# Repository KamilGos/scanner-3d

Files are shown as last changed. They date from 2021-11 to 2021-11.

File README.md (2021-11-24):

<!-- image -->
<div align="center" id="top"> 
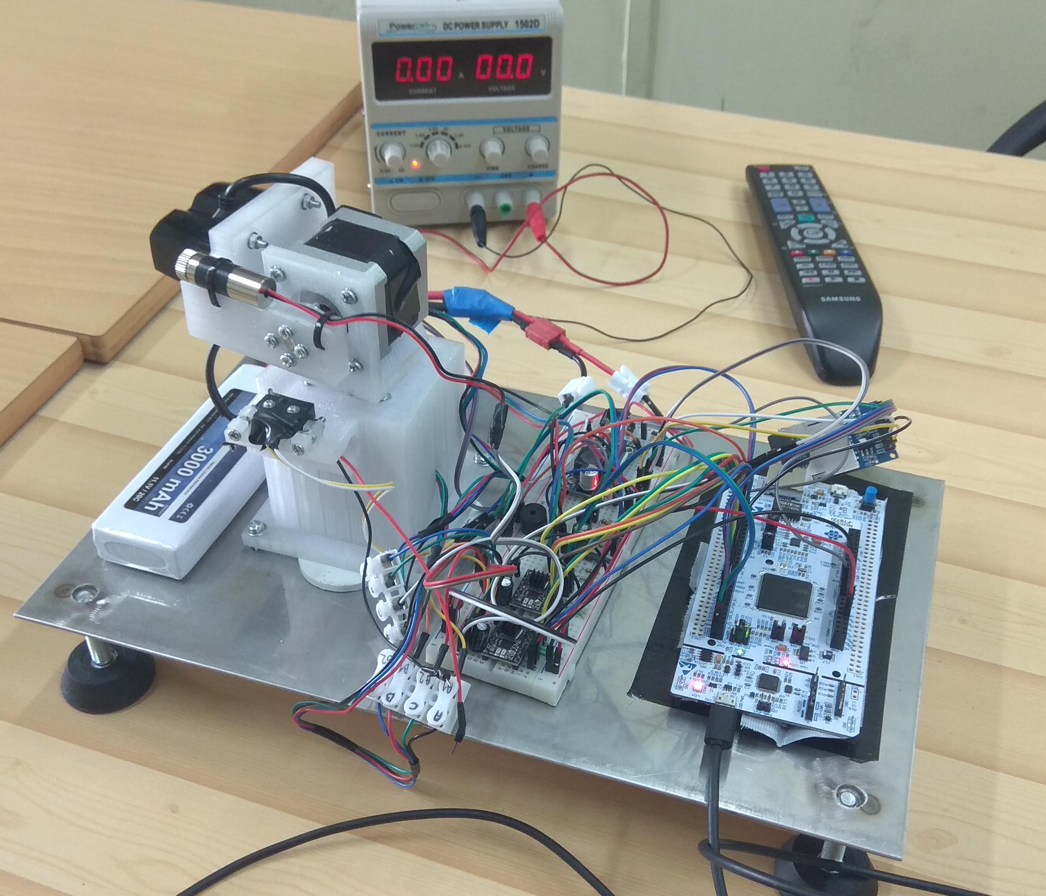
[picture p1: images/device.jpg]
  
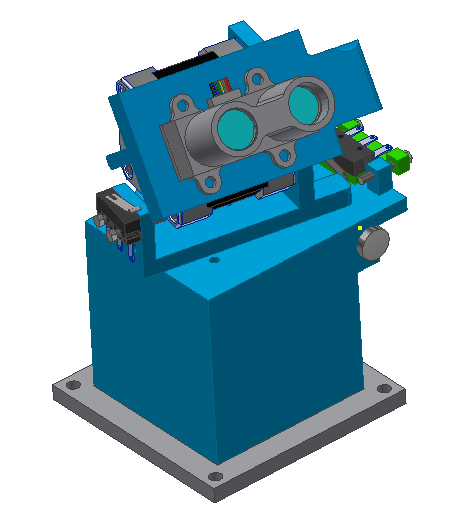
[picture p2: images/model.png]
  
  &#xa0;
</div>

<h1 align="center"> scanner-3d </h1>
<h2 align="center"> Lidar-based 3D environment scanner - generate a point cloud! </h2>

<!-- https://shields.io/ -->
<p align="center">
  
  
  
</p>

<!-- table of contents -->
<p align="center">
  <a href="#dart-about">About</a> &#xa0; | &#xa0;
  <a href="#package-content">Content</a> &#xa0; | &#xa0;
  <a href="#eyes-implementation">Implementation</a> &#xa0; | &#xa0;
  <a href="#microscope-tests">Tests</a> &#xa0; | &#xa0;
  <a href="#memo-license">License</a> &#xa0; | &#xa0;
  <a href="#technologist-author">Author</a> &#xa0; | &#xa0;
</p>

<br>

## :dart: About ##
The aim of the project is to create a device that allows scanning any surface to 3d model.

The process is based on spot distance measurement. To measure the distance the lidar is used. It ensures sufficient accuracy and the range of measurements. 

The basic structure consists of a Lidar mounted on the effector of a manipulator with two degrees of freedom. The whole electronics is based on a static metal structure. The measurements are visualized in a computer application which also provides necessary operations such as Poisson reconstruction. 

<h2>Principle of operation</h2>
The manipulator consists of two degrees of freedom, each rotating by 180 degrees, which allow the measurement of the semi-spherical space above the device. The active element ensuring the rotation of each axis is a stepper motor. Measurements are performed on average every 2ms. Each time after receiving a measurement from Lidar, the microcontroller converts the obtained distance, taking into account the angular position of the effector, into Cartezian coordinate system. The angles that are used to convert the values are updated with each rotation of the shaft of any motor. After the measurement process is completed, the data is transferred to a stationary station, where one make an initial decimation by removing gross errors with the help of a script. Subsequently, using an open-source program (like https://www.meshlab.net/ ), it is possible determine normal vectors for each measurement point, thanks to which we are able to use Poisson smoothing to reconstruct the measurement surface.

<br>

<div align="center" id="top"> 
  
  &#xa0;
</div>

<br>

## :package: Content
 * [CAD/3d_printing](CAD/3d_printing) - STL files for 3d-printing
 * [CAD/sacnner.stp](CAD/scanner.stp) - STEP file with model
 * [examples](examples) - two exmaple files with point clouds genereted with described device
 * [schematic](schematic) - pdf and sch schematics of electronics model
 * [sources](sources) - code for microcontroller

## :eyes: Implementation ##
The mapping algorithm can be explained in the following way:

1. The upper motor takes steps until the upper limit switch sends a signal to the microcontroller. It goes back and performs micro-steps until the upper limit switch sends a signal to the microcontroller for precise alignment.
2. The lower motor does the same as the upper motor for the lower limit switch.
3. The lower motor performs 1 micro step.
4. The top motor performs 1 micro step.
5. Lidar takes a distance measurement and sends it to the microcontroller.
6. Converting distances to coordinates (x, y, z) in the microcontroller
7. The upper motor carries out the remaining micro-steps by performing steps 5 and 6 of the algorithm.
8. Measurements are saved on the SD card in the format (x, y, z).
9. The lower motor carries out the remaining micro-steps by performing steps 3-8

## :microscope: Tests ##
Many scans have been performed, which indicate that the device makes sense and its further development may bring beneficial results. The scans from the examples folder are presented below:

<h2>Example 1 - part of room<h2>
<div align="center">

| Name | Figure |
|--- | --- |
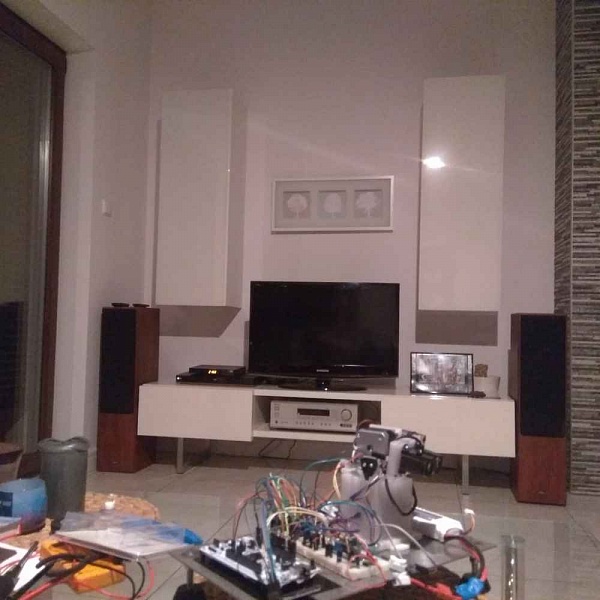
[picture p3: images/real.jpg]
| Real view  |   |
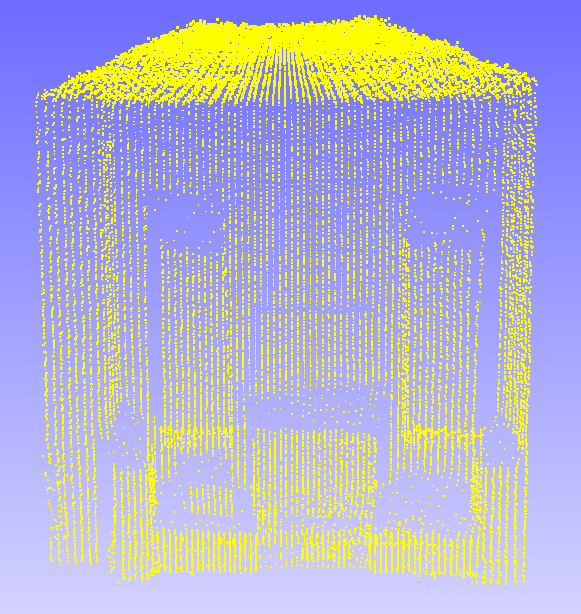
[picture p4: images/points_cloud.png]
| Points cloud  |   |
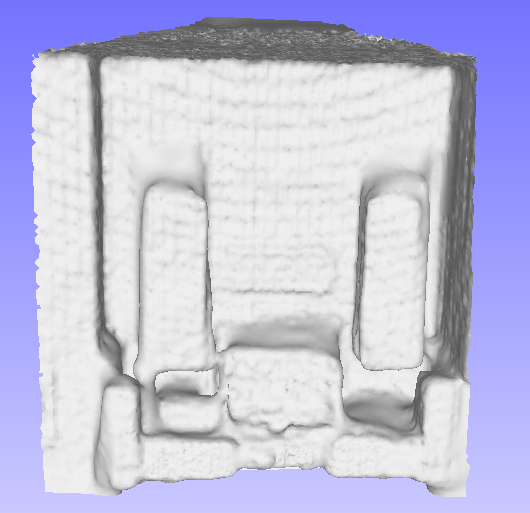
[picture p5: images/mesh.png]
| Poisson reconstruction  |   |
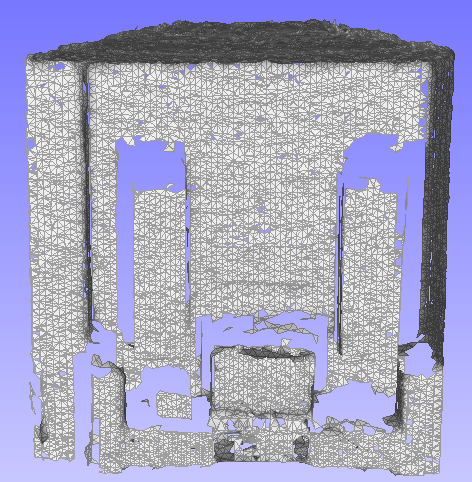
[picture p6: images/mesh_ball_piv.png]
| Ball pivoting reconstruction|   |

</div>

<h2>Example 2 - whole room<h2>
<div align="center">

| Name | Figure |
|--- | --- |
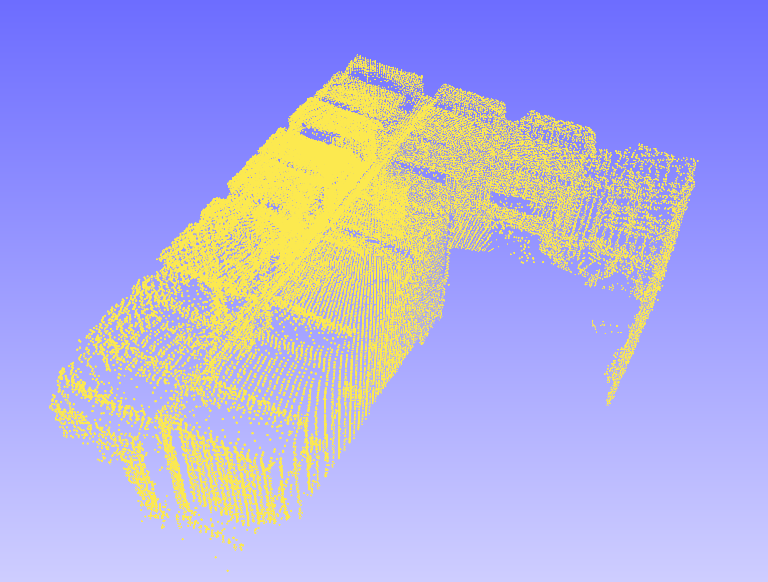
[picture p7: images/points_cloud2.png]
| Points cloud |   |

</div>

## :memo: License ##

This project is under license from MIT.

## :technologist: Author ##

Made with :heart: by <a href="https://github.com/KamilGos" target="_blank">Kamil Goś</a>

&#xa0;

<a href="#top">Back to top</a>

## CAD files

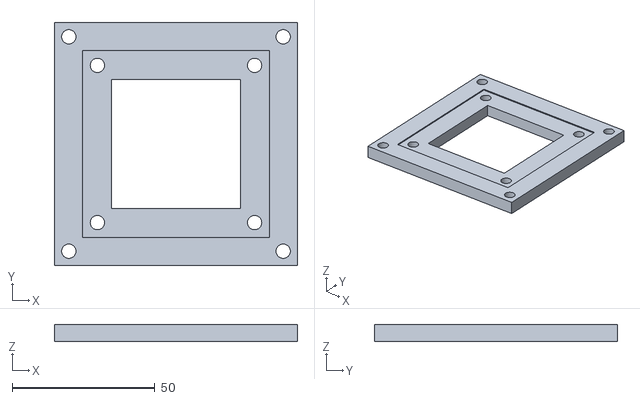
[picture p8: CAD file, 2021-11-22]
CAD/3d_printing/part1.stl
85.0 x 85.0 x 6.00

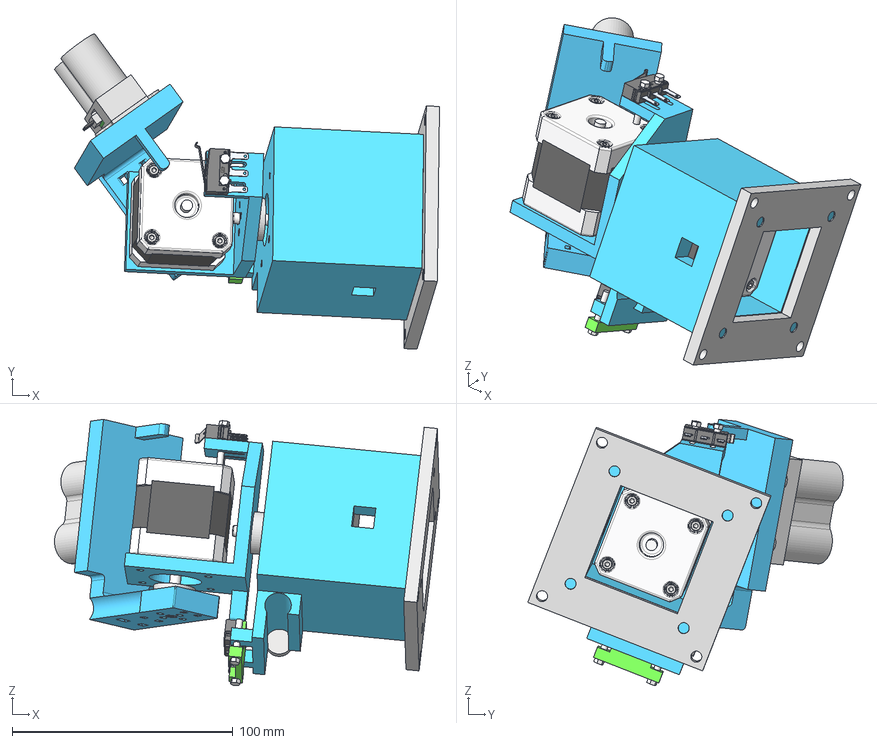
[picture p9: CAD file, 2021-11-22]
CAD/scanner.stp
174.3 x 142.8 x 120.5 mm
LIDAR
Nema 17 Base x 2
Nema 17 Body x 2
Nema 17 Top x 2
Nema 17 Shaft x 2
ISO 4762 - M2.5 x 6 x 8
stepper_hub x 2
uchwyt_na_lidar
uchwyt_miedzy_steperami
uchwyt_stepera_do_podstawy
limit_switchMicroswitch-SS-3GL13SL
M3x19 x 4
limit_switch2Microswitch-SS-3GL13SL
laser

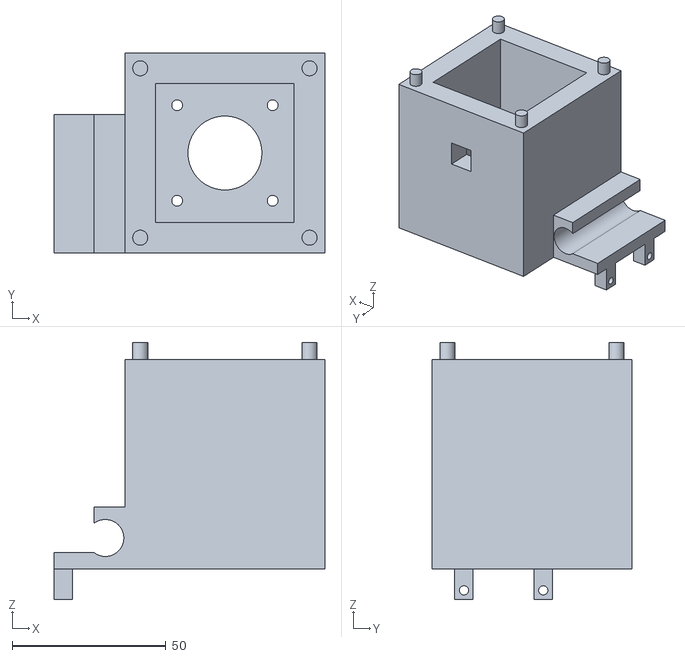
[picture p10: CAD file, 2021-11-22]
CAD/3d_printing/part2.stl
88.0 x 65.0 x 83.5

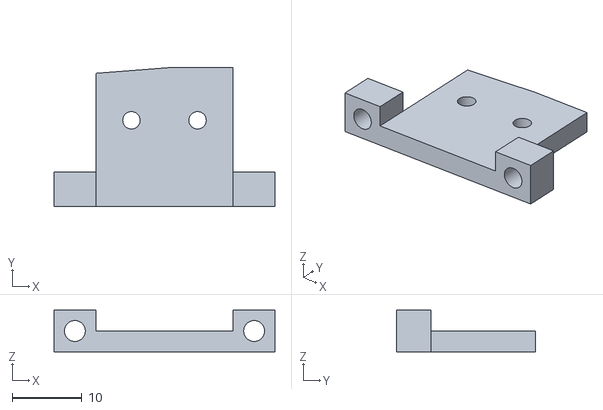
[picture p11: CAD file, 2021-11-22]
CAD/3d_printing/part3.stl
31.8 x 20.0 x 6.00

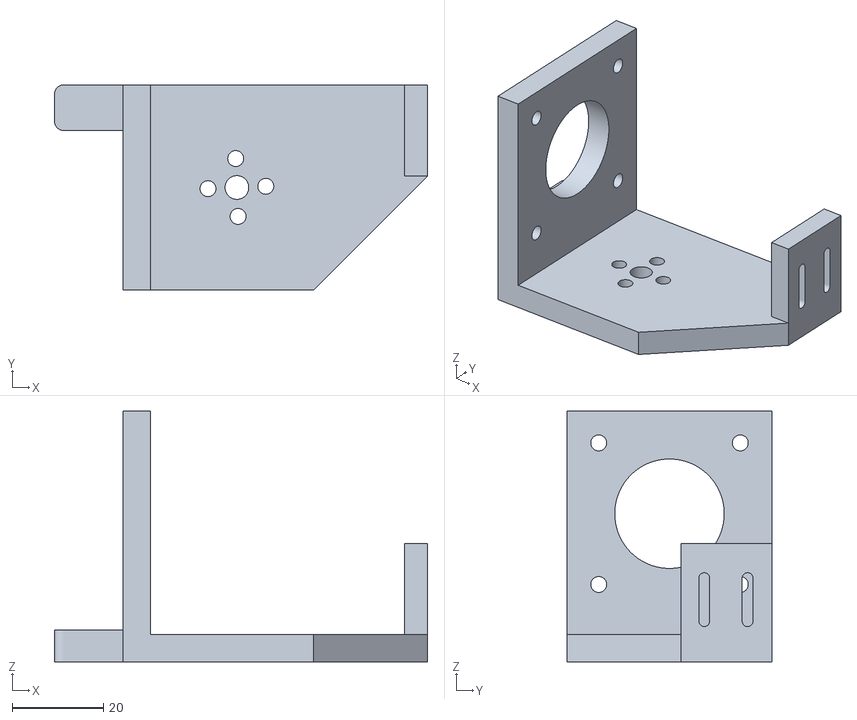
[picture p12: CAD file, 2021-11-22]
CAD/3d_printing/part4.stl
81.8 x 45.0 x 55.0

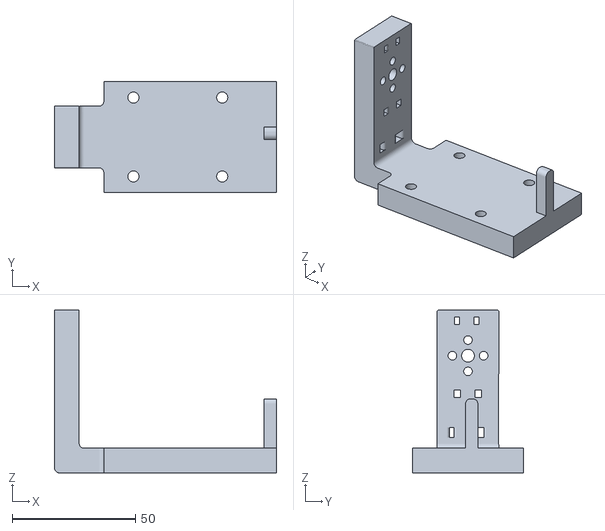
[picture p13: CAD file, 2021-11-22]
CAD/3d_printing/part5.stl
90.0 x 45.0 x 66.0

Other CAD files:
examples/ex1.ply
examples/ex2.ply

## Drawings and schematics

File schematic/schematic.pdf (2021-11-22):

# 10k ¹⁰k 10k

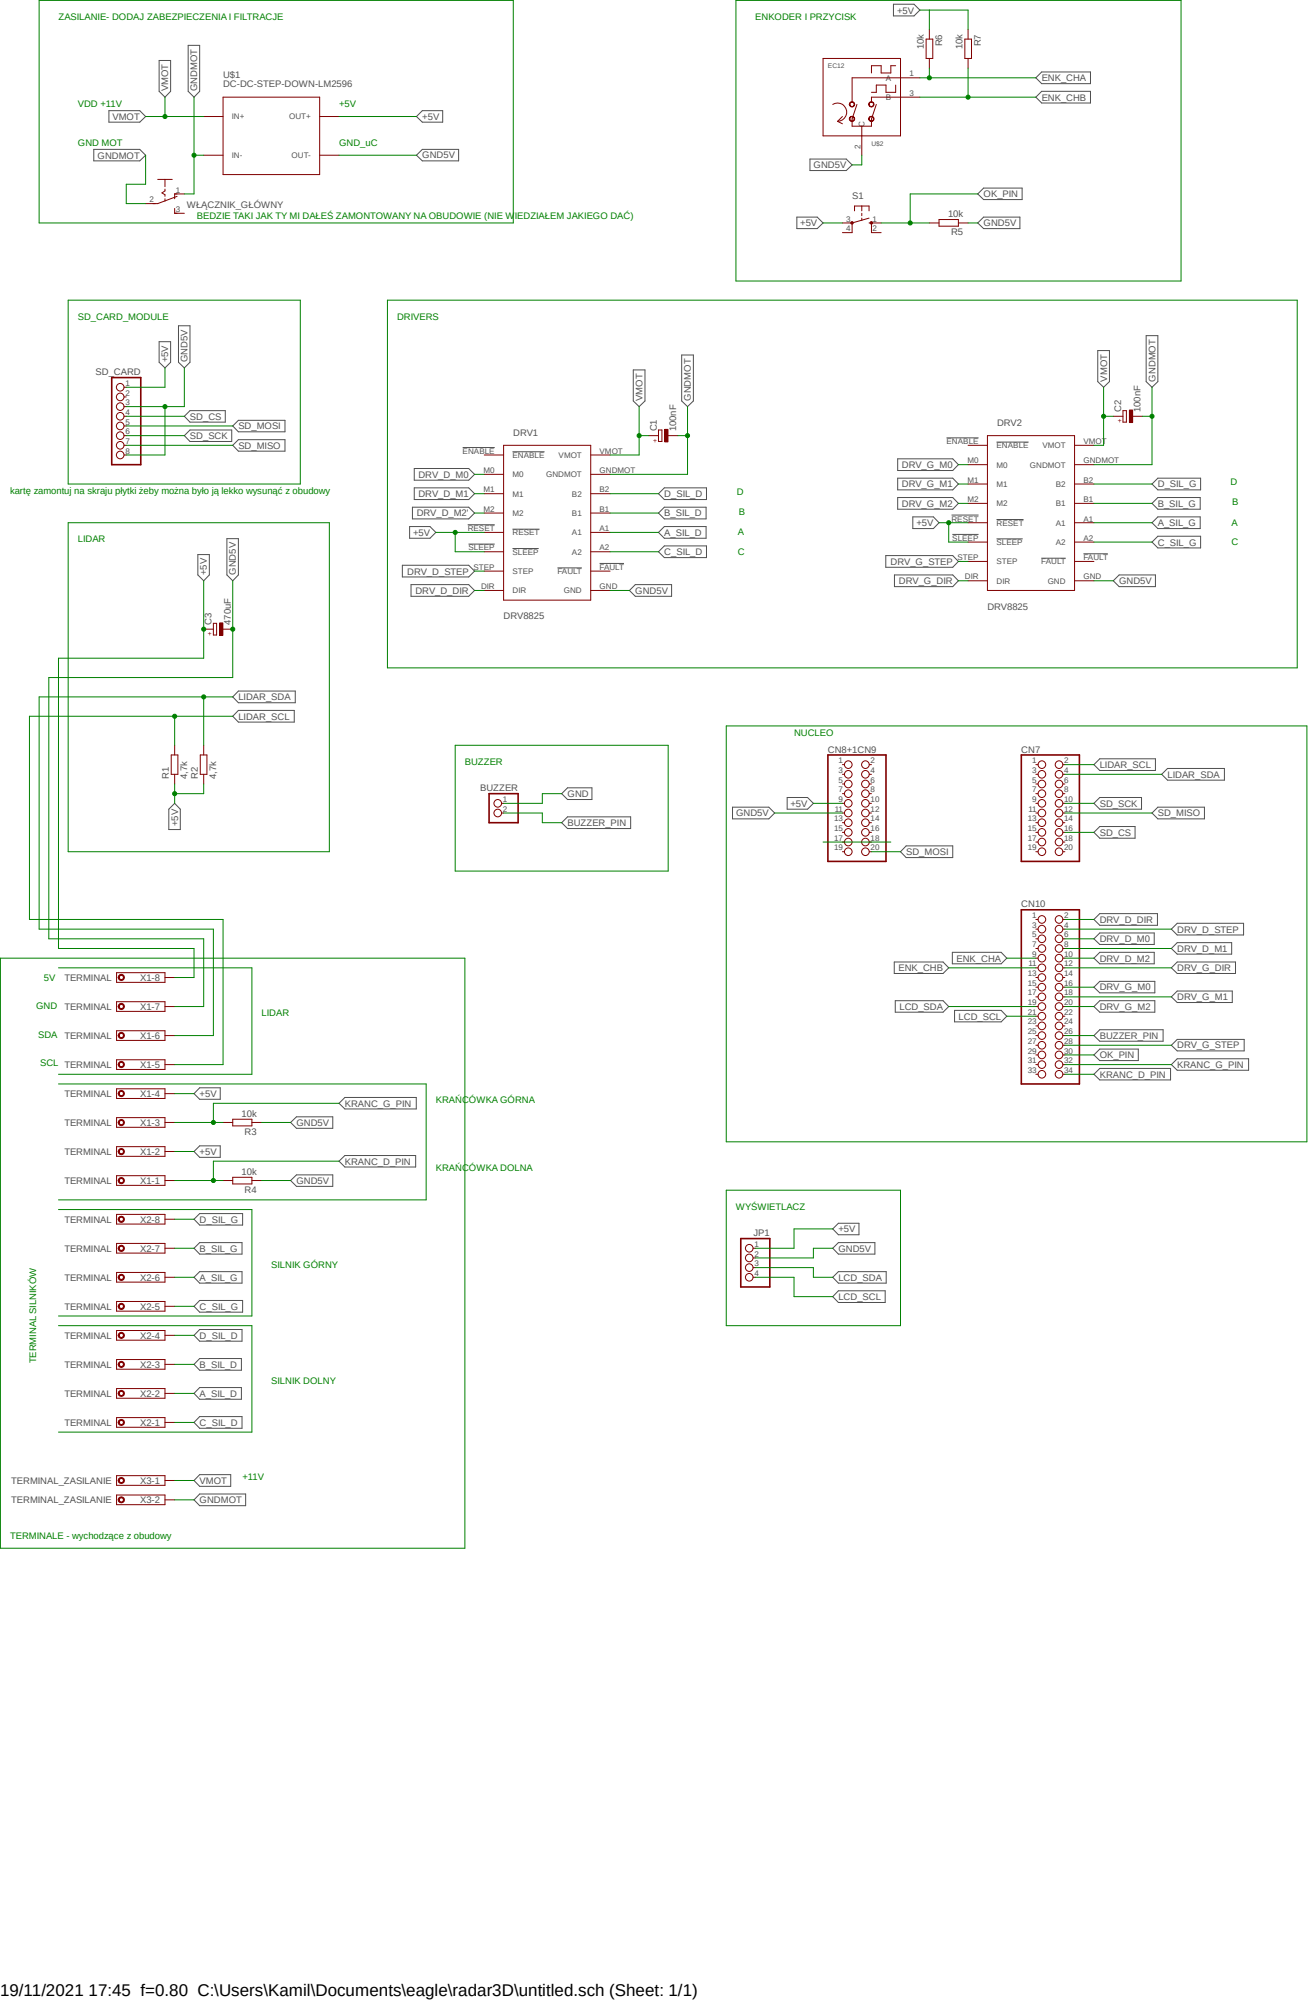
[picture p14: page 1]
DRV8825; DC-DC-STEP-DOWN-LM2596; 4,7k TERMINAL TERMINAL TERMINAL TERMINAL TERMINAL TERMINAL TERMINAL TERMINAL; TERMINAL_ZASILANIE; ENABLE ENABLE; RESET RESET; SLEEP SLEEP; STEP STEP; DIR DIR; VMOT; VMOT GNDMOT; GNDMOT B2; A2 FAULT; FAULT GND; GND; DRV1; DRV2; OUT+ OUT- U$1; BUZZER 1; SD_CARD 1 2 3 4 5 6 7 8; 4 VMOT VMOT; D_SIL_D; B_SIL_D; A_SIL_D; C_SIL_D; D_SIL_G; B_SIL_G; A_SIL_G; C_SIL_G; GND5V; GND5V GND⁵V GND⁵V; GND5V GND5V; GND5V GNDMOT; GNDMOT; LIDAR_SDA; LIDAR_SCL; SD_MOSI; SD_SCK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

ZASILANIE- DODAJ ZABEZPIECZENIA I FILTRACJE

VDD +11V GND MOT

1 WŁĄCZNIK_GŁÓWNY
BEDZIE TAKI JAK TY MI DAŁEŚ ZAMONTOWANY NA OBUDOWIE (NIE WIEDZIAŁEM JAKIEGO DAĆ)

kartę zamontuj na skraju płytki żeby można było ją lekko wysunąć z obudowy

TERMINAL TERMINAL TERMINAL TERMINAL

TERMINALE - wychodzące z obudowy TERMINAL SILNIKÓW

19/11/2021 17:45 f=0.80 C:\Users\Kamil\Documents\eagle\radar3D\untitled.sch (Sheet: 1/1)
